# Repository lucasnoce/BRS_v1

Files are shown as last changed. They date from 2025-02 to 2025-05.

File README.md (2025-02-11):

# Basic Rocketry System

This repo will be used to develop a basic system for rocketry avionics. Development is still in initial phase, as described below, and will most definetly go under many changes and tweeks as the project evolves.

For updated project information, please refer to the [**General Requirements document**](Documentation/General_Requirements.pdf). The images and descriptions in this README may be out of date.

# Rocketry Overview
## My Background
I am a recently graduated Electronics Engineer and a space/rocketry enthusiast. For 3 years during graduation, I participated on a student rocketry team (at the time called Beyond Rocket Design, now Beyond Aerospace Department) where I helped to design and build model rockets for competitions like LASC, FBMF and so many others.

The problem is I knew nothing about rocketry back then (I still don't for the most part but hey, at least I have some xp now) and I was just starting to learn electronics, so although I knew how to code a little bit, I had never even heard of things like RTOS, threads, drivers and many many other things. Back then we used to program on Arduino IDE and created some really basic pcbs with ATmega328 and, later, ESP32 DevKit. Nothing wrong with that, we were able get somethings working, but of course my imagination never stops thinking about how much faster, reliable and efficient I could make those systems had I implemented them with some fancier techniques.

So, this is my main motivation for this project. I will be trying to implement an avionics system that does the basic but does it well. And obviously, if it works I will also try to convince the current team members to let me fly this thing on one of their rockets.

## Flight Behavior
Suborbital model rockets tend to (although, more often than desired, they don't) go through these 6 main stages during flight:
- Lift off
- Powered Ascent
- Coasting / Unpowered Ascent
- Parachute / Recovery system deployment
- Slow Descent
- Landing

<p align="center">
  <br>Flight Stages
  <br>Flight Stages (NASA)
  <br>Source: NASA's <a href="https://www1.grc.nasa.gov/beginners-guide-to-aeronautics/flight-of-a-model-rocket/" target="_blank">Beginners Guide to Aeronautics</a>
</p>
<!-- ![rktflight](https://github.com/user-attachments/assets/89e4ac4f-ced1-4a4b-8422-af78ff70ac67) -->

<p align="center">
  <br>Flight Stages: force analysis
  <br>Flight Stages Resultant Analysis
  <br>Source: Image created by the author
</p>
<!-- ![flight_stages](https://github.com/user-attachments/assets/95ef7178-a636-40cd-b9dc-83a80c350e83) -->

Notice that the most important events that happen during a flight - as far as software development goes - are the transitions between stages:
- Launch: transition from being still and moving, hopefully, upwards
- Main Engine Cut-Off (MECO): transition from Powered to Unpowered Ascent
- Apogee: transition from moving upwards to downwards
- Parachute: transition from descending almost on free fall to descending slowly
- Landing: transition from descending to - we expect - softly stopping on the ground

Consider that the avionics system will have some kind of IMU (Inertial Measurement Unit), which basically tells us the instantaneous acceleration along its 3 axes. It will also feature a barometric sensor to measure the air pressure during flight. Now, let's imagine a rocket flying without any rotation, so that the Z-axis is always pointing up (this will never actually happen, but it's good for demonstration purposes). We can plot a graph with the approximate resultant acceleration (in red) and the corresponding velocity (in green) during this flight.

<p align="center">
  <br>Flight Behavior: acceleration (red) and velocity (green)
  <br>Flight Behavior
  <br>Source: Image created by the author
</p>
<!-- ![desmos-graph](https://github.com/user-attachments/assets/daaf0ec1-653c-4937-aa67-dafecf62db17) -->

As we can see in this simplified example, the resultant acceleration starts at 0g (1g = 9.8 m/s^2). It rises up to about 5g and then falls back down to 0g. This period where the acceleration is positive corresponds to the powered ascent, as illustrated on the previous image. Note that the rocket hits its maximum velocity when the acceleration is 0 (of course, since a=dv/dt). Then, the vehicle experiences free fall for some time (a = -1g) until the parachutes are deployed, at around T+28 seconds. From this point, the rocket falls at a constant speed only to hit the ground at T+41 seconds.

Just to be very clear, this example is absolutely, completely inaccurate and overly simplified. In practice, the acceleration curve of the motor during powered ascent stage is much steeper and shorter and the free fall period should be significantly smaller. Also, this example ignores any kind of air resistance, which is definetely not a great idea when studying rockets. However, I hope the example helps us understand the overall behavior of a model rocket during flight.

# Project Requirements and definitions

For updated project information, please refer to the [**General Requirements document**](Documentation/General_Requirements.pdf). The images and descriptions in this README may be out of date.

## Hardware
The main objective with this project is to develop the device firmware, so hardware requirements are being defined based on components I have easy access to, mainly some off-the-shelf modules. If everything goes well after prototyping, I might review the project and design some proper hardware for it, but for now it is what it is.

## Firmware
First of all, I defined a [State Machine](Documentation/FW%20State%20Machine.png) to control the system behavior based on rockect flight phases. For this project, I considered that the parachute shall be deployed on apogee detection in order to simplify things a little. This machine will be managed by the Flight Control thread, shown in the [Architecture](Documentation/FW%20Architecture.png) structure below.

<p align="center">
  <br>FW State Machine
  <br>FW State Machine
  <br>Source: Image created by the author
</p>
<!-- ![FW State Machine](https://github.com/user-attachments/assets/7c7314bc-370f-4cdf-bbdf-a78096dcc1fc) -->

Basically, the system is initialized on the first state and, if everything is working properly, moves to S1 where the operation mode is selected based on a mechanical switch state. There are only 2 modes: UART mode is used to select secondary opModes (such as reading post-flight data and configuring the system) and Flight mode is where the magic happens.

A flight only starts after the Remove Before Flight tag is detected as removed. This has many reasons, in this case the most important being reliability, since this helps prevent a false flight start, as well as saving battery power. After that, the system has 4 detection states, one for each flight stage transition. For example, S3 keeps trying to detect lift off stage by analyzing IMU and barometric sensor data. Another example is S4, which tries to detect MECO by also analysing data from IMU and barometric sensor, or (for redundancy) can move forward after a certain timeout.

After landing has been detected (and if the rocket is still a rocket) the system tries to backup the data from internal flash to a secondary storage unit, which may be a microSD card or another flash chip (still to be defined). Finally, the system goes to S8, a state designed to facilitate rocket recovery (sometimes, they really like hiding underground) while also saving battery power. In this state, the system stays on a cycle of sleeping and waking up to beep/blink the buzzer/LEDs until the battery is critically low.

All of this is operation is illustrated in the following [Flowchart](Documentation/FW%20Flowchart.png) (also under development).

<p align="center">
  <br>FW Flowchart
  <br>FW Flowchart
  <br>Source: Image created by the author
</p>
<!-- ![FW Flowchart](https://github.com/user-attachments/assets/43fa580d-00c4-4f8f-b531-e44d9dea57e4) -->

Lastly, the system will be organized according to the following [Architecture](Documentation/FW%20Architecture.png) (yes, you guessed it, this is also not the final version).

<p align="center">
  <br>FW Architecture
  <br>FW Architecture
  <br>Source: Image created by the author
</p>
<!-- ![FW Architecture](https://github.com/user-attachments/assets/24211131-3822-4550-bf50-66789afae103) -->

## Tests and Validation
Untested rocket code is bad rocket code. So, I need a good way of testing this firmware to validate individual blocks and also the complete system working together. Of course, the biggest issue here is that I don't have multiple rockets to fire up and watch what happens. I am still not sure how to do this (if you have any ideas or advices, please tell me), but I fell like what I need is a combination of these 2 things:
1. Simulated flight data: a piece of code that simulates a flight by generating coherent sensor data and feeds it into the system firmware as inputs.
2. Small scale test flight: some sort of physical structure tied to my device/pdb that allows me to through it up the air and control the descent phase so that it doesn't crash onto the ground.

First method is clearly safer, but doesn't provide a "real world" condition. Second method allows me to test things in conditions closer to a real flight, but may lead to a lot of frustration, electronic waste and emptiness in my wallet. For now though, I will focus on developing the main firmware and some sort of flight simulation function.

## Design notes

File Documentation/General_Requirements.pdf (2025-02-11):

# Basic Rocket System v1.0

## General Requirements and Specification

Rev 01
2025

Lucas Arturo Noce
lucasnoce0@gmail.com
https://github.com/lucasnoce/BRS_v1

Table of Contents

List of Figures

List of Tables

### 1. Document overview

1.1. Introduction

The Basic Rocket System (BRS) is an open source device designed - as a side personal project - to implement all the most basic functionalities expected from a model rocket avionics computer.
The focus of the project is on firmware development, as hardware is heavily dependent on the rocket structure and design. However, firmware does not exist without hardware, so a block diagram and electrical schematic will be sketched. The system will be designed to feature some basic functionalities and also to be compatible with future software and, especially, hardware upgrades that can provide further utilities for the system.
1.2. Scope

This document aims to clearly define all the BRS requirements, such as hardware and firmware structure, and also describe guidelines of how the system should perform and be built.
In this document, some main hardware components will also be specified to allow firmware development to be started. The complete electrical schematic and PCB layout are topics for another document.
1.3. Disclaimer

This project is designed by me, Lucas, as a personal project. It is not intended for commercial purposes nor any other use rather than model rocketry hobby activities.
This project is open-source under the MIT license, allowing the community to explore and contribute. However, I disclaim any responsibility for any misuse, damage, or consequences resulting from the use of this project. Do it at your own risk.
Rockets can be seriously dangerous - and potentially deadly - for the ones involved, for others and nearby strangers, so be very cautious, conservative and safe when exploring the rocketry world.

### 2. Hardware Requirements

2.1. MoSCoW Analysis

The definition of HW specification started by listing all the components related to a standard avionics system. Then, the MoSCoW prioritisation method was implemented in order to enumerate the necessary and desired components. The criteria used to categorize each component was completely arbitrary, but focused on maintaining the lowest possible cost while also allowing the device to have all the key features needed for a basic avionics system.

Table 1 - Hardware Components MoSCoW Analysis

Hardware Component | MoSCoW | Comments
MCU | Must Have | Focus on low power and/or low cost
IMU | Must Have | Periodically sample acceleration and gyro
Barometer | Must Have | Apogee detection
Power Tree | Must Have | Includes power source, probably LiPo batteries
Recovery System | Must Have | For triggering parachute deployment
Data logging | Must Have | Primarily flash chip, maybe microSD card for cost reduction
Remove Before Flight | Must Have | Must be removed with the rocket fully assembled
LEDs | Must Have | Indicate system state
Backup System | Should Have | May not be designed for cost reduction
Buzzer | Should Have | Indicate system state
GPS | Should Have | May not be used for cost reduction
Wireless Communication | Should Have | Will likely be added later, probably LoRa P2P
Camera | Could Have | Really increases system complexity and storage demand, may be added later as a separate system
Self Ignition System | Could Have | Depends on rocket motor design

Because of the mentioned criteria, some important components were categorized as “Should Have” or even “Could Have” to reduce costs. But, as the project evolves, some of them may be added on later versions of the system.
After the MoSCoW analysis, the components chosen to integrate the project are the following:
- MCU
- IMU

- Barometer
- Power Tree
- Recovery System
- Data logging
- Remove Before Flight
- LEDs
- Buzzer
2.2. Components Specification

Considering that the device will not be mass produced, many components were chosen based on availability, meaning that the focus on low power and/or low cost are often more dependent on retailers stock than on datasheet information.

### 2.2.1. MCU

For the MCU, the following options were considered. Component information was sourced from the corresponding datasheet. Average price is an approximate value taken from local stores.

Table 2 - MCU Options

Manufacturer | Part # | Flash / RAM (bytes) | Max Clock (MHz) | Consumption (mA@freqmax) | Average Price
STMicroelectronics | STM32F103C8 | 64k / 20k | 72 | 50 | R$ 30,00
STMicroelectronics | STM32F103RB | 128k / 20k | 72 | 50 | R$ 100,00
STMicroelectronics | STM32F401CC | 256k / 64k | 84 | 22 | R$ 45,00
STMicroelectronics | STM32F411CE | 512k / 128k | 100 | 23.6 | R$ 55,00
Espressif | ESP32-WROOM-32 | 4M / 520k | 240 | 80 | R$ 40,00

Data driven analysis indicates that the best option (low cost, high density) would be the ESP32. However, previous experiences were also considered and I happen to not be a huge fan of the Espressif platform. Besides, the datasheet shows an average current consumption of 80 mA, which is the highest value amongst the options.
The second best component seems to be the STM32F411CE, which has enough flash memory to store data from one entire flight and the largest RAM compared to the remaining options. That, alongside presenting almost a quarter of the current consumption than the ESP32, has made this the selected MCU.

### 2.2.2. IMU

For the IMU, the following options were considered. Component information was sourced from the corresponding datasheet. Average price is an approximate value taken from local stores.

Table 3 - IMU Options

Manufacturer | Part # | DOF | Max Acc ODR (Hz) | Max Acc Range | Supply Voltage | Consumption | Bus | Average Price
NXP | MMA8452 | 3 | 800 | ±8g | 2.0~3.6V | <165 μA | I2C | R$ 20,00
InvenSense | MPU6050 | 6 | 1k | ±16g | 2.4~3.4V | <3.9 mA | SPI / I2C | R$ 30,00
STM | LSM6DS3 | 6 | 1.6k | ±16g | 1.7~3.6V | <900 μA | SPI / I2C | R$ 20,00
Bosch | BNO055 | 9 | 100 | ±16g | 2.4~3.6V | <12.3mA | I2C / UART | R$ 300,00

The first version will use an MPU6050 for its good overall balance of features and cost, as well as being a fairly common and off the shelf option. That said, later versions may switch to the LSM6DS3, as it seems to be a little more adequate for the task based on having a greater ODR and lower current consumption, while maintaining a similar price.

### 2.2.3. Barometer

Table 4 - BAR Options

Manufacturer | Part # | Pressure Resolution | Pressure Range (hPa) | ODR (Hz) | Consumption | Bus | Average Price
Bosch | BMP180 | 1 Pa | 300~1100 | 120 | <12 μA | SPI / I2C | R$ 10,00
Bosch | BMP280 | 0.16 Pa | 300~1100 | 157 | <2.8 μA | SPI / I2C | R$ 20,00
Bosch | BME280 | 0.18 Pa | 300~1100 | 182 | <2.8 μA | SPI / I2C | R$ 20,00
STM | LPS22HH | 0.02 Pa | 260~1260 | 200 | <4 μA | SPI / I2C | R$ 6,00

The first version will use a BMP280 for its good overall balance of features and cost, as well as being a fairly common and off the shelf option. That said, later versions may switch to the LPS22HH, as it seems to be a little more adequate for the task based on having a greater ODR and similar current consumption and price.

### 2.2.4. Power Tree

The Power Tree (PWT) is actually a subcircuit that contains all power supply components, as well as the control signals and other power related items. As of the first version of this system, the PWT block diagram is as follows. The red arrows indicate power delivery traces and the grey ones indicate signal traces.

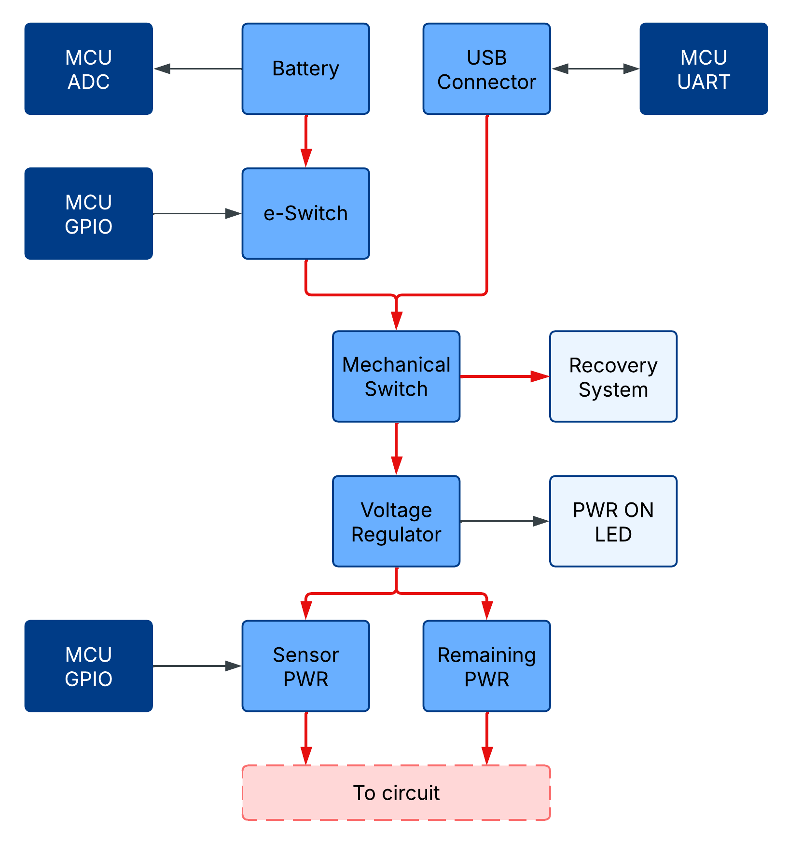
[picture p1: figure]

Figure 1 - Power Tree block Diagram

The subcircuit provides two ways of powering the device: internal battery and USB connector. To prevent issues with both power sources connected at the same time, protective diodes must be added accordingly and an SMD solder jumper should be added to allow physical disconnection of the USB power line to the system, still granting serial communication through GND and UART traces.
The internal battery must be able to provide the voltage and current necessary to the system through the whole flight process, including the periods between system power up and the actual vehicle launch and between landing and physical recovery of the rocket. Both of these periods are unknown beforehand and prone to several minutes or hours of delay, depending on a variety of factors such as weather conditions, unexpected on-site issues, etc.
With that in mind, it is important to calculate, simulate and test a large number of scenarios in order to correctly specify the minimum battery capacity needed, which will only be possible to do reliably after the whole system is working properly. Thus, the current capacity of the internal battery will be defined later on. The voltage however, depends on two main factors: the voltage regulator constraints and the recovery system design. The first factor will probably not be an issue, as the voltage regulator selected will most certainly be a switching regulator, which typically accepts a wide range of input voltage.
The recovery system design can vary a lot. In my previous experience, this system was quite unusual and deployed the parachutes from a side door on the body of the rocket without the use of any explosive. Instead, it used some electromagnets to hold a metal piece fixated on the side door. This design is interesting for not using explosives, but continuously drains current from the power supply to keep the doors closed and also requires higher voltages to properly activate the electromagnets.
A more common approach is to divide the rocket into two (or more) parts and position the parachutes on the nose cone. Some sort of explosive is then used to separate these parts and deploy the recovery system. In this method, despite having some associated risk related to the explosive, the power demand is significantly smaller, since the system only uses power momentarily to ignite the explosive.
There are plenty of other designs and philosophies regarding recovery systems. To simplify things a little, this project will use a 12V battery source, which is a fairly common value and may be compatible with most recovery system designs.
Back to the PWT subcircuit, some details are important to guarantee a successful flight and to improve avionics system handling on a fully assembled rocket. For that, the PWT design shall follow the guidelines:
- ON/OFF mechanical switch must be accessible from outside with the rocket fully assembled;
- PWT subcircuit shall not feature battery charging for the sake of simplicity;
- USB connector shall be either type C (preferably) or microB;
- A solder jumper must be added to select between power sources, i.e. a jumper footprint on the USB power line right before the Mechanical Switch, effectively allowing the disconnection of the USB power supply;
- The system must implement a self-shutdown feature controlled by MCU, through the e-Switch;
- The voltage regulator must be able to provide enough power for all transient events that are known;
- It is advisable that the implemented regulator follows a switching topology for better overall performance;
- The MCU must be able to control the power delivery (ON/OFF) to the “sensors” (IMU, BAR and backup flash);

### 2.2.5. Recovery System

// TODO

### 2.2.6. Storage

The first analysis that needs to be done regarding a storage solution is to estimate how much data a typical flight will generate. To do that, the following data structure is considered, taking into consideration the selected sensors characteristics.

Table x - Components Summary

Component | Data | Type | Unit | Estimate Size (bytes)
MCU | Timestamp | uint32_t | ms | 4
MCU | Flight State | uint8_t | - | 1
MCU | Device Status | uint8_t | - | 1
MCU | Battery Voltage | uint16_t | mV | 2
IMU | Accelerometer | uint16_t [3] | raw | 6
IMU | Gyroscope | uint16_t [3] | raw | 6
BAR | Pressure | uint8_t [3] | raw | 3
BAR | Temperature | uint8_t [3] | raw | 3
Total | | | | 26

// TODO

### 2.2.7. Remove Before Flight

// TODO
- Must be accessible from outside, i.e. with the rocket fully assembled
- Must be possible to reinsert the tag with the rocket fully assembled

### 2.2.8. LEDs and Buzzers

To define the number of LEDs necessary to the system, the following reasoning was presented:
- FW predicts a total of 11 states on State Machine, so a 4 LEDs can display the current state (for debugging only, they may be removed for flight)
- 1 LED for power input indication (purely HW, may be removed for flight)
- 1 LED for low battery indication
- At least 2 more LEDs for other indications and debugging

With this in mind, a total of 8 LEDs can comfortably handle all the needs of the system. Since one of them is not controlled by the MCU, there are 7 LEDs left to be controlled. Using one dedicated GPIO for each LED is poor use of resources and can lead to unnecessary future constraints on the hardware side, so a better option is to control the LEDs through an I2C IO Expander. And because these ICs typically provide a power-of-two number of IOs, one more LED will be added to complete 8 controlled LEDs and 1 uncontrolled LED.
For the expander, some options were considered and the selected IC was the TCA9534A by Texas Instruments, since it provides all the needs for this task as well as being the cheapest option.
The buzzer, on the other hand, can’t be efficiently used through an IO Expander, since it requires PWM output for better control. Hence, it will be connected to a dedicated PWM-capable GPIO. Also, only one buzzer will be used, since there are only 3 use cases predicted, which don’t interfere with each other:
- Signaling RBF
- Facilitate recovery process (keeps beeping after landing)
- Low battery indication

Finally, it is worth noting the suggestion to add a low pass filter between the PWM GPIO and the buzzer input to increase sound quality.

### 2.2.9. Components Summary

Finally, a summary of all selected components and corresponding specification is presented below. This list is still not a Bill Of Materials, so only the most important components are shown.

Table x - Components Summary

Component | Specification
MCU | STM32F411CE
IMU | MPU6050
BAR | BMP280
Power Tree | 12V battery, USB, ON/OFF switches
Recovery | // TODO
Backup Flash | // TODO
RBF | // TODO
LEDs | 8 LEDs through TCA9534A IO expander
Buzzer | 1 buzzer
2.3. Block Diagram

Based on the selected components, a high abstraction block diagram was designed to help visualize the circuits. Grey arrows indicate signal traces, while the green ones indicate high voltage and red ones low voltage power delivery traces.

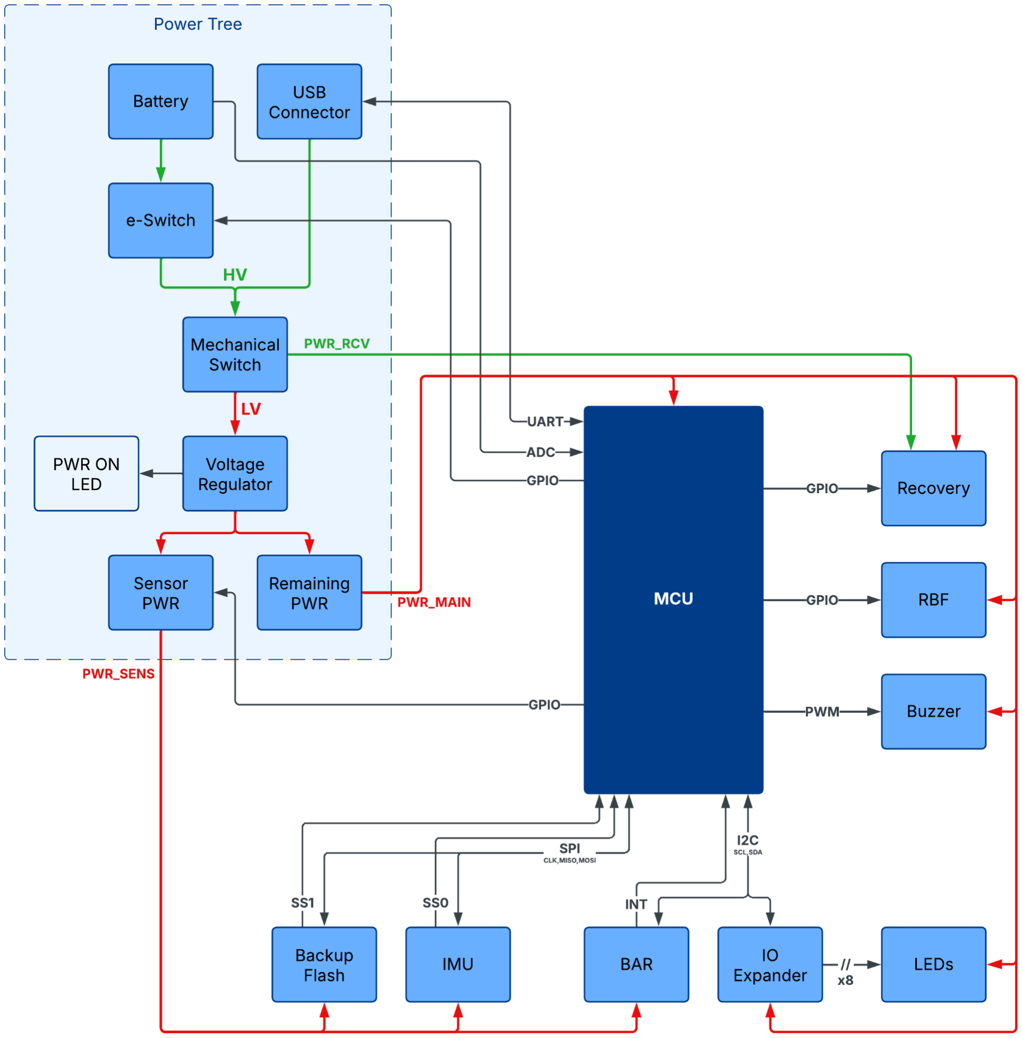
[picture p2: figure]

Figure 2 - Circuit Block Diagram

### 3. Software Requirements

3.1. State Machine

A state machine was created to better organize and control the device under all the possible flight stages and implement other functionalities.

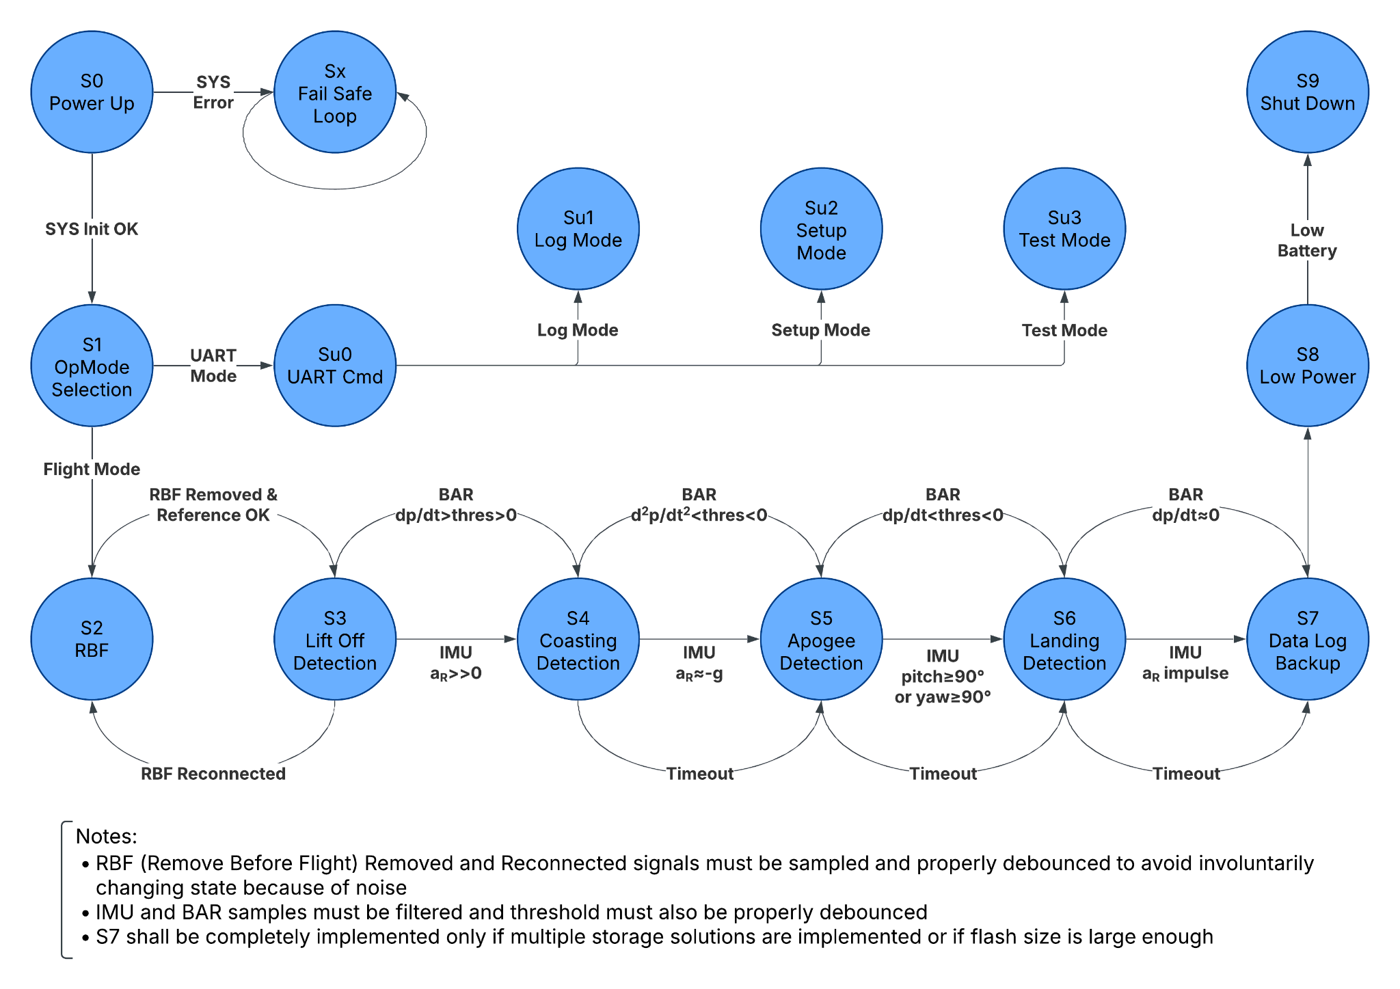
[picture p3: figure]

Figure 3 - System State Machine

### 3.1.1. S0 - Power Up

This is the first state of the system after being powered up. It carries the responsibility of initializing all the drivers and services necessary for device operation.
Since the system can wake up after a variety of events - and, therefore, have valuable data stored in flash memory - the S0 state is also responsible for reading some system status information from flash and deciding how to move forward with the operation from a safety perspective. It should be able to detect, for example, if the system is booting up mid flight after some unexpected shutdown has happened and after that, try to resume operation from the previously known state.

### 3.1.2. S1 - OpMode Selection

This state is responsible for determining the selected operation mode based on a physical switch/jumper. There are 2 operation modes:
- Flight mode corresponds to a secondary state machine which tracks the flight stages based on sensor readings. It consists of states S2 through S7.
- UART mode is meant to select between the secondary operation modes through custom AT commands.

The operation mode selection is designed this way (mixing hardware and software selections) to minimize the chance of an undesired operation mode swap during flight caused by vibration. This design only allows the selection of a secondary mode (Sun

) when the hardware selection jumper is wired correctly.

### 3.1.3. S2 - Remove Before Flight

This state is the first step of the flight mode. It continuously tries to identify if the Remove Before Flight (RBF) tag has been removed, indicating that the vehicle is completely assembled and ready to launch. This is done by polling the corresponding RBF GPIO input value and getting the RBF removed value for many times in a row.
Also in this state, right after the RBF removal is detected, some reference measures are taken and used as a starting point for the flight, such as vehicle attitude (inclination of the rocket), vehicle orientation (the axes with the largest acceleration magnitude), ground level pressure, etc. These measures must be successfully completed in order for the machine to advance to the next state, otherwise it must indicate this error and stop the launch procedure for vehicle inspection and system reboot.

### 3.1.4. S3 - Lift Off Detection

After S2 is completed, the machine enters a lift off detection state. In this state, the system effectively starts to read, interpret and store data from the sensors continuously with the objective of detecting the motor ignition. These are the possible signals that can trigger a state change (in order of priority):
- RBF reconnected: if the RBF is reconnected, the system will understand it as a launch hold and return to the previous state (S2).
- IMU resulting acceleration values show a sudden and intense increase in magnitude while also inverting the signal value of the vertical orientation axes (previously determined).
- BAR readings show a sudden, intense and consistent decrease in magnitude, indicating a sequential drop in pressure, thus a rise in altitude.

### 3.1.5. S4 - Coasting Detection

After successfully detecting lift off, the system moves to S4 which aims to detect the ending of powered ascent and beginning of coasting phase. For this to happen, these triggers are considered (in order of priority):
- IMU resulting acceleration values show a consistent decrease in magnitude (tending to the previously determined baseline value of approximately -1g) while also inverting the signal value of the vertical orientation axes again.
- BAR readings show a growing decrease in magnitude (approximately constant decrease of second derivative), indicating a sequential drop in pressure, thus a rise in altitude
- A coasting detection timeout occurs (empirically determined and implemented in pre-compile time).

### 3.1.6. S5 - Apogee Detection

After successfully detecting coasting, the system moves to S5 which aims to detect apogee, i.e. the ending of ascent and beginning of descent phase. For this to happen, these triggers are considered (in order of priority):
- BAR readings show a consistent increase in magnitude, indicating a sequential rise in pressure, thus a drop in altitude. Can also be understood as a change in slope signal of the pressure variation.
- IMU gyroscope values show an absolute rotation above 90° in pitch (θ) or yaw (φ), not considering rotation around the previously determined vertical orientation axes, roll (ζ).
- An apogee detection timeout occurs (empirically determined and implemented in pre-compile time).

### 3.1.7. S6 - Landing Detection

After successfully detecting apogee, the system moves to S6 which aims to detect landing. For this to happen, these triggers are considered (in order of priority):

- BAR readings show consistently similar magnitude values, indicating steady pressure levels, thus a stable and constant altitude.
- IMU resulting acceleration values show a short impulse magnitude (full scale) followed by constant values of around 1g.
- A landing detection timeout occurs (empirically determined and implemented in pre-compile time).

### 3.1.8. S7 - Data Log Backup

After landing detection, the system enters Data Log Backup state, which can be skipped if there are no backup storage devices detected. This state copies the contents of the internal storage into the backup storage for redundancy and ease of access, especially if the backup device is an SD card.

### 3.1.9. S8 - Low Power

After backing up the stored flight data, the system goes to Low Power state, where it deinitializes all the unnecessary drivers and services and enters a light sleep loop. In this loop, the device keeps blinking an indication LED and beeping the buzzer for some period to help find the vehicle on the recovery mission.
This loop continues until a low voltage threshold is reached on the ADC readings of the internal battery. After that, the machine moves to the S10 state.

### 3.1.10. S9 - Shut Down

In this state, the system executes a self-shutdown procedure. This procedure triggers a MOSFET to essentially disconnect the internal battery (main power source during flight) from the power supply line, which turns the device completely off.

### 3.1.11. Sx - Fail Safe

This is a fail safe state, designed to safely and reliably manage system initialization errors, allowing unexpected behavior to be handled in a controlled and harmless way.

### 3.1.12. Su0 - UART Command

This state corresponds to UART Command, which allows the user to select between the secondary operation modes through custom serial port AT commands.

### 3.1.13. Su1 - Log Mode

This state corresponds to a read-only state where stored flight data can be safely accessed and retrieved from internal and/or backup storage.

### 3.1.14. Su2 - Setup Mode

This state allows the user to set up the device configuration.

### 3.1.15. Su3 - Test Mode

This state is meant to be used as a Test mode for the device, yet to be completely defined.

3.2. Flowchart

Based on the state machine, the following firmware flowchart was designed.

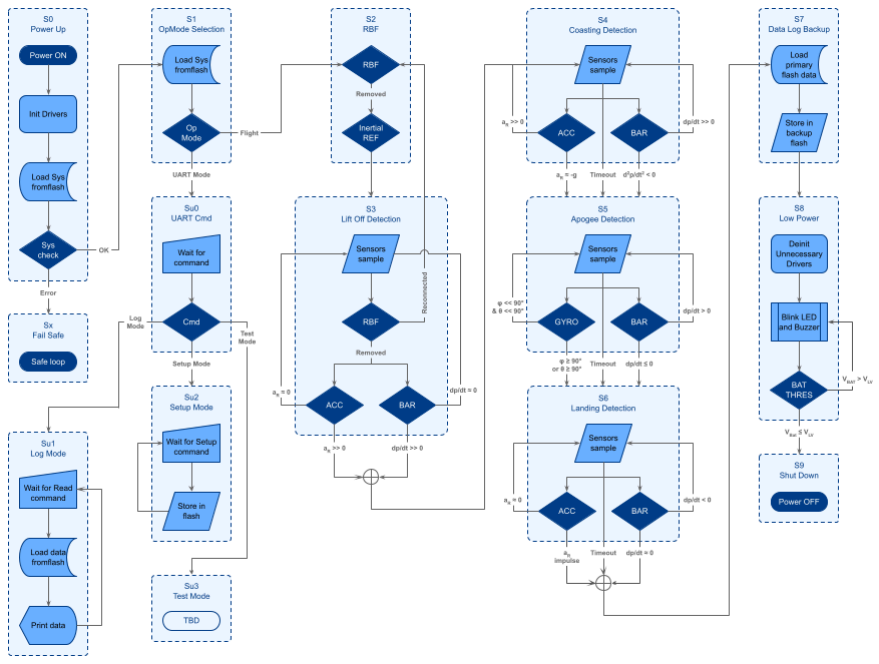
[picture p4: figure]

Figure 4 - Firmware Flowchart

3.3. Firmware Architecture

The firmware abstraction layers are organized as illustrated below. The MCU HAL layer is provided by STM32CubeMX and allows the use of MCU hardware. Above the MCU HAL, a Board Support Package provides an isolation layer between the BRS and hardware specific functions, essentially granting a high level of compatibility between the whole software above and almost any other MCU with minimal driver refactoring.
The Drivers layer implements all the necessary drivers for the suggested hardware approach mentioned in the previous section. This layer is then consumed by the Services layer, which manages all the necessary activities needed. Finally, a high level Application layer implements the designed state machine. Between the Services and Application layers is the Inter Process Communication service which provides a messaging system for threads of both layers to communicate through. The RTOS used will be FreeRTOS.

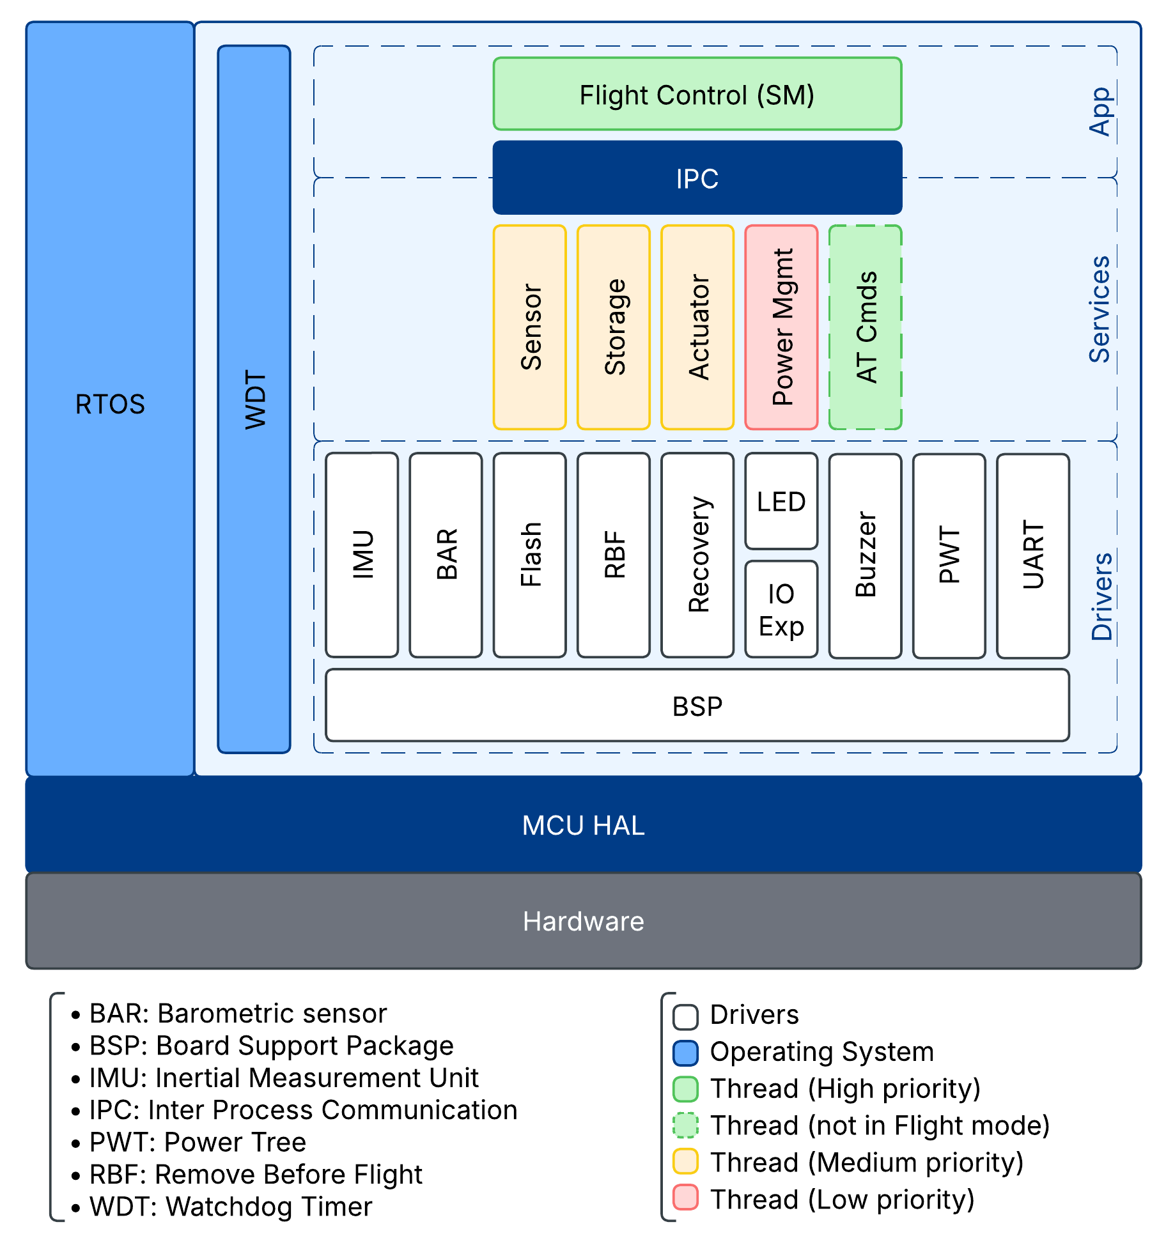
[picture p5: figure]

Figure 5 - Firmware Layer Architecture

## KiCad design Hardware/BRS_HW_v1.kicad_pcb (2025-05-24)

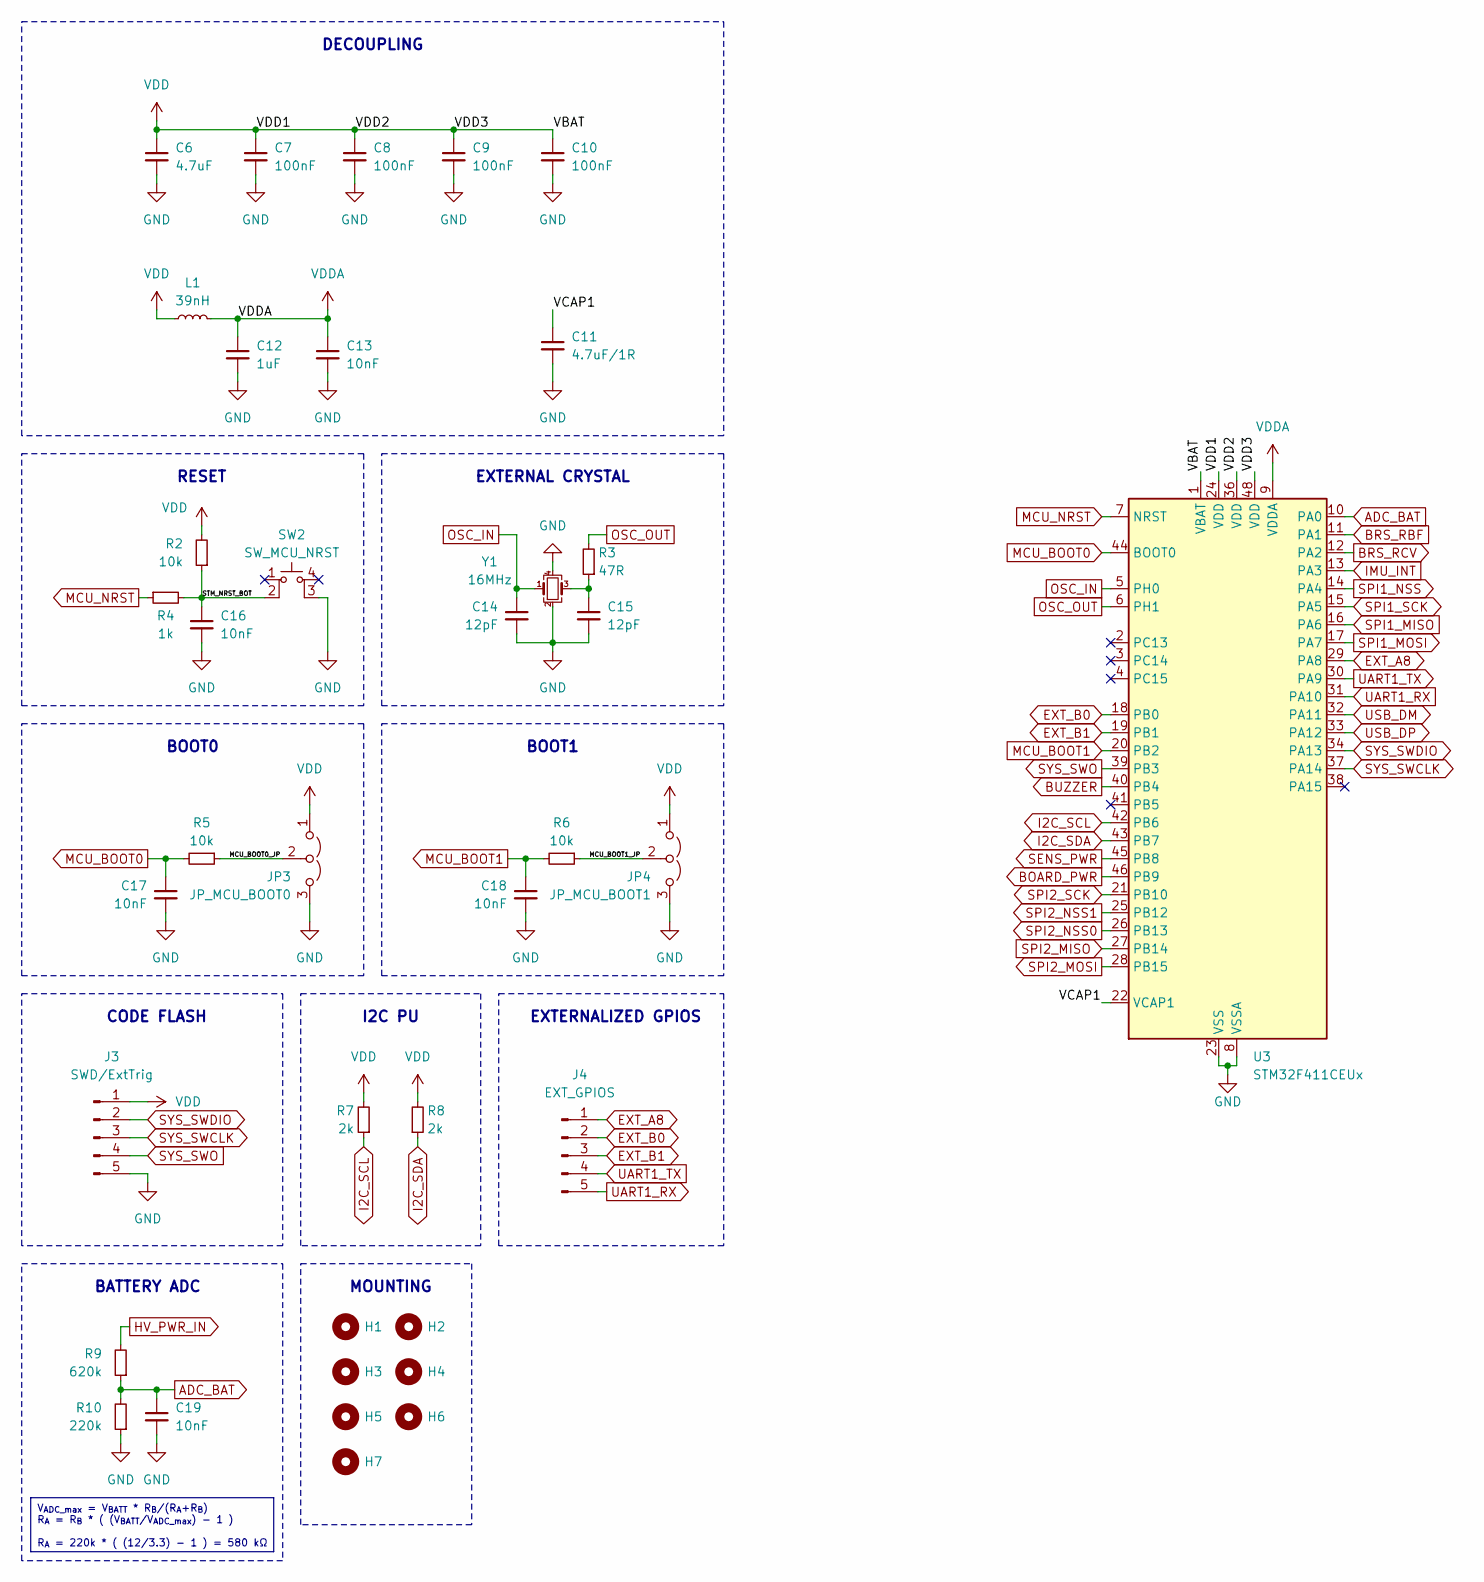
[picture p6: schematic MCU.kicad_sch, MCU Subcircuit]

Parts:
C6: 4.7uF; C_0603_1608Metric; LCSC Part Number C19666
C7, C8, C9, C10: 100nF; C_0402_1005Metric; LCSC Part Number C1525
C11: 4.7uF/1R; C_0603_1608Metric; LCSC Part Number C57112
C12: 1uF; C_0402_1005Metric; LCSC Part Number C52923
C13: 10nF; C_0402_1005Metric; LCSC Part Number C15195
C14, C15: 12pF; C_0402_1005Metric; LCSC Part Number C1547
C16, C17, C18, C19: 10nF; C_0603_1608Metric; LCSC Part Number C57112
H1, H3, H5, H7: SupPCB; MountingHole_2.2mm_M2_DIN965
H2, H4, H6: ToolingHole; JLCPCB_Tooling_Hole
J3: SWD/ExtTrig; PinHeader_1x05_P2.54mm_Vertical
J4: EXT_GPIOS; PinHeader_1x05_P2.54mm_Vertical
JP3: JP_MCU_BOOT0; SMD_SolderJumper_Triple_Small
JP4: JP_MCU_BOOT1; SMD_SolderJumper_Triple_Small
L1: 39nH; L_0603_1608Metric
R2, R5, R6: 10k; R_0603_1608Metric; LCSC Part Number C25804
R3: 47R; R_0402_1005Metric; LCSC Part Number C25120
R4: 1k; R_0603_1608Metric; LCSC Part Number C21190
R7, R8: 2k; R_0402_1005Metric; LCSC Part Number C22975
R9: 620k; R_0603_1608Metric; LCSC Part Number C22975
R10: 220k; R_0603_1608Metric; LCSC Part Number C22975
SW2: SW_MCU_NRST; SW_TS-1187A-B-A-B; LCSC C318884
U3: STM32F411CEUx; QFN-48-1EP_7x7mm_P0.5mm_EP5.6x5.6mm
Y1: 16MHz; Crystal_SMD_Abracon_ABM8G-4Pin_3.2x2.5mm; LCSC Part Number C13738

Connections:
/MCU/MCU_BOOT0_JP: JP3.2 (C), R5.1
/MCU/MCU_BOOT1_JP: JP4.2 (C), R6.1
/MCU/STM_NRST_BOT: C16.1, R2.1, R4.2, SW2.2
/MCU/VCAP1: C11.1, U3.22 (VCAP1)
ADC_BAT: C19.1, R9.1, R10.2, U3.10 (PA0)
BOARD_PWR: U3.46 (PB9); also elsewhere on the board
BRS_RBF: U3.11 (PA1); also elsewhere on the board
BRS_RCV: U3.12 (PA2); also elsewhere on the board
BUZZER: U3.40 (PB4); also elsewhere on the board
EXT_A8: J4.1, U3.29 (PA8)
EXT_B0: J4.2, U3.18 (PB0)
EXT_B1: J4.3, U3.19 (PB1)
GND: C6.2, C7.2, C8.2, C9.2, C10.2, C11.2, C12.2, C13.2, C14.2, C15.2, C16.2, C17.2, C18.2, C19.2, J3.5, JP3.3 (B), JP4.3 (B), R10.1, SW2.3 (K), U3.8 (VSSA), U3.23 (VSS), U3.35 (VSS), U3.47 (VSS), U3.49 (VSS), Y1.2, Y1.4; also elsewhere on the board
HV_PWR_IN: R9.2; also elsewhere on the board
I2C_SCL: R7.1, U3.42 (PB6); also elsewhere on the board
I2C_SDA: R8.1, U3.43 (PB7); also elsewhere on the board
IMU_INT: U3.13 (PA3); also elsewhere on the board
MCU_BOOT0: C17.1, R5.2, U3.44 (BOOT0)
MCU_BOOT1: C18.1, R6.2, U3.20 (PB2)
MCU_NRST: R4.1, U3.7 (NRST)
unnamed: C15.1, R3.1, Y1.3
OSC_IN: C14.1, U3.5 (PH0), Y1.1
OSC_OUT: R3.2, U3.6 (PH1)
SENS_PWR: U3.45 (PB8); also elsewhere on the board
SPI1_MISO: U3.16 (PA6); also elsewhere on the board
SPI1_MOSI: U3.17 (PA7); also elsewhere on the board
SPI1_NSS: U3.14 (PA4); also elsewhere on the board
SPI1_SCK: U3.15 (PA5); also elsewhere on the board
SPI2_MISO: U3.27 (PB14); also elsewhere on the board
SPI2_MOSI: U3.28 (PB15); also elsewhere on the board
SPI2_NSS0: U3.26 (PB13); also elsewhere on the board
SPI2_NSS1: U3.25 (PB12); also elsewhere on the board
SPI2_SCK: U3.21 (PB10); also elsewhere on the board
SYS_SWCLK: J3.3, U3.37 (PA14)
SYS_SWDIO: J3.2, U3.34 (PA13)
SYS_SWO: J3.4, U3.39 (PB3)
UART1_RX: J4.5, U3.31 (PA10)
UART1_TX: J4.4, U3.30 (PA9)
USB_DM: U3.32 (PA11); also elsewhere on the board
USB_DP: U3.33 (PA12); also elsewhere on the board
VDD: C6.1, C7.1, C8.1, C9.1, C10.1, J3.1, JP3.1 (A), JP4.1 (A), L1.1, R2.2, R7.2, R8.2, U3.1 (VBAT), U3.24 (VDD), U3.36 (VDD), U3.48 (VDD); also elsewhere on the board
VDDA: C12.1, C13.1, L1.2, U3.9 (VDDA)

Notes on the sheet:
V_{ADC_max} = V_{BATT} * R_{B}/(R_{A}+R_{B}) R_{A} = R_{B} * ( (V_{BATT}/V_{ADC_max}) - 1 ) R_{A} = 220k * ( (12/3.3) - 1 ) = 580 kΩ
BOOT1
MOUNTING
CODE FLASH
EXTERNAL CRYSTAL
I2C PU
DECOUPLING
BOOT0
EXTERNALIZED GPIOS
BATTERY ADC
RESET

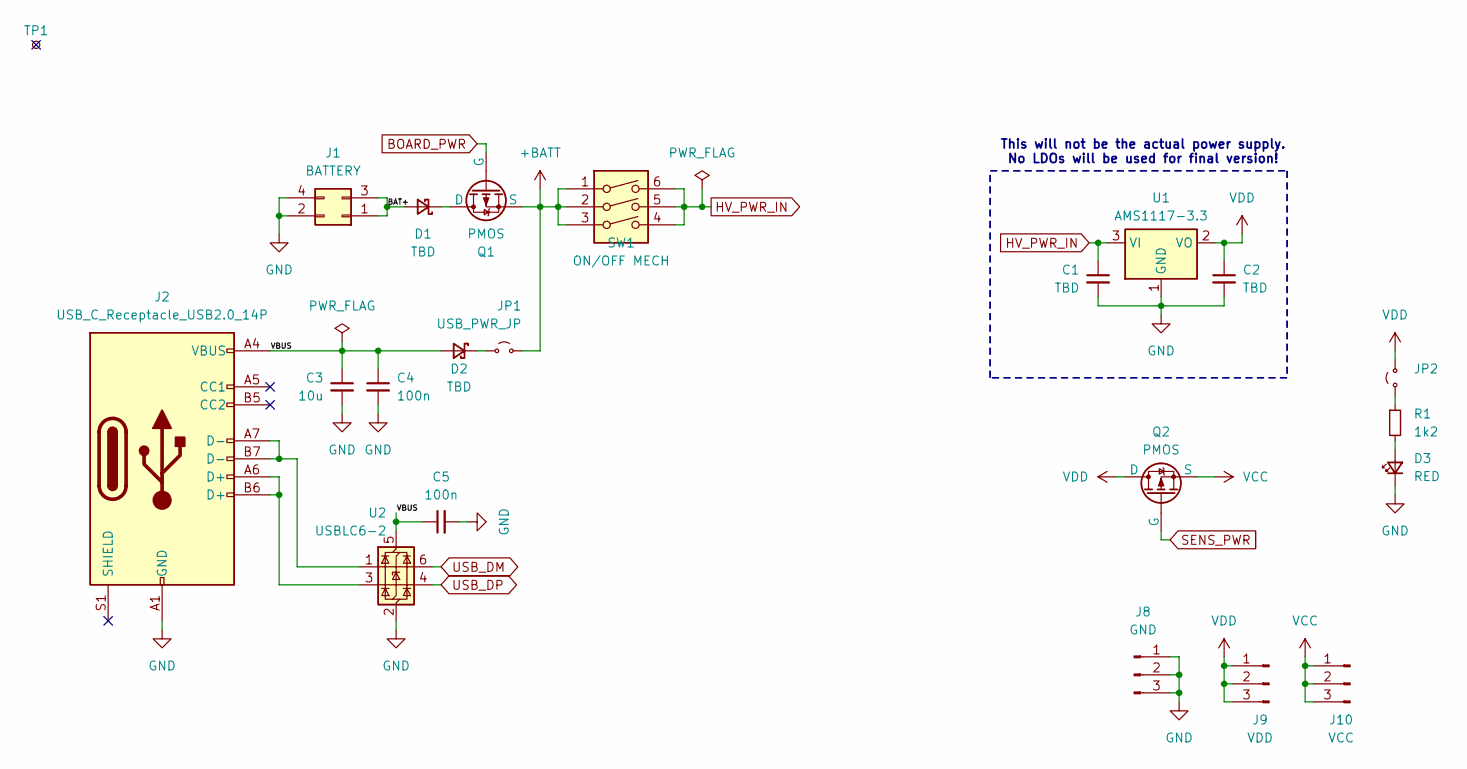
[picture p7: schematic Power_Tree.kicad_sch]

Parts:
C1, C2: TBD; C_0603_1608Metric
C3: 10u; C_0603_1608Metric
C4, C5: 100n; C_0603_1608Metric
D1, D2: TBD; D_SOD-123
D3: RED; LED_0603_1608Metric
J1: BATTERY; Molex_Micro-Fit_3.0_43045-0412_2x02_P3.00mm_Vertical
J2: USB_C_Receptacle_USB2.0_14P; USB_C_Receptacle_GCT_USB4105-xx-A_16P_TopMnt_Horizontal
J8: GND; PinHeader_1x03_P2.54mm_Vertical
J9: VDD; PinHeader_1x03_P2.54mm_Vertical
J10: VCC; PinHeader_1x03_P2.54mm_Vertical
JP1: USB_PWR_JP; SolderJumper-2_P1.3mm_Open_RoundedPad1.0x1.5mm
JP2: Jumper_2_Small_Open; SMD_SolderJumper_Small
Q1, Q2: PMOS; SOT-23
R1: 1k2; R_0603_1608Metric
SW1: ON/OFF MECH; SW_DIP_SPSTx03_Slide_6.7x9.18mm_W7.62mm_P2.54mm_LowProfile
TP1: TestPoint_Small; TestPoint_Pad_D1.5mm
U1: AMS1117-3.3; SOT-223-3_TabPin2
U2: USBLC6-2; SOT-23-6

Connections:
+BATT: JP1.2 (B), Q1.3 (S), SW1.1, SW1.2, SW1.3
/Power_Tree/BAT+: D1.2 (A), J1.1, J1.3
/Power_Tree/VBUS: C3.1, C4.1, C5.1, D2.2 (A), J2.A4 (VBUS), J2.A9 (VBUS), J2.B4 (VBUS), J2.B9 (VBUS), U2.5 (VBUS)
BOARD_PWR: Q1.2 (G); also elsewhere on the board
GND: C1.2, C2.2, C3.2, C4.2, C5.2, D3.1 (K), J1.2, J1.4, J2.A1 (GND), J2.A12 (GND), J2.B1 (GND), J2.B12 (GND), J8.1, J8.2, J8.3, U1.1 (GND), U2.2 (GND); also elsewhere on the board
HV_PWR_IN: C1.1, SW1.4, SW1.5, SW1.6, U1.3 (VI); also elsewhere on the board
unnamed: D1.1 (K), Q1.1 (D)
unnamed: D2.1 (K), JP1.1 (A)
unnamed: D3.2 (A), R1.2
unnamed: J2.A6 (D+), J2.B6 (D+), U2.3 (I/O2)
unnamed: J2.A7 (D-), J2.B7 (D-), U2.1 (I/O1)
unnamed: JP2.1 (A), R1.1
SENS_PWR: Q2.2 (G); also elsewhere on the board
USB_DM: U2.6 (I/O1); also elsewhere on the board
USB_DP: U2.4 (I/O2); also elsewhere on the board
VCC: J10.1, J10.2, J10.3, Q2.3 (S); also elsewhere on the board
VDD: C2.1, J9.1, J9.2, J9.3, JP2.2 (B), Q2.1 (D), U1.2 (VO); also elsewhere on the board

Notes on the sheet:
This will not be the actual power supply. No LDOs will be used for final version!

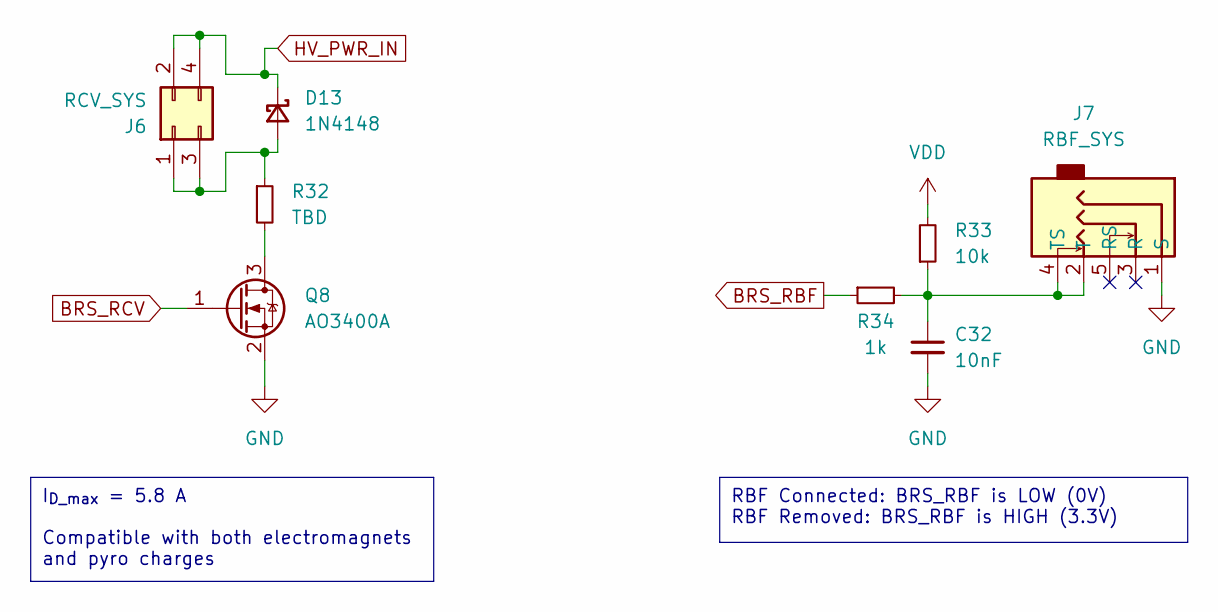
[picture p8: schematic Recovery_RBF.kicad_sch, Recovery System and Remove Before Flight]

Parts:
C32: 10nF; C_0603_1608Metric; LCSC Part Number C57112
D13: 1N4148; D_SOD-123
J6: RCV_SYS; Molex_Micro-Fit_3.0_43045-0412_2x02_P3.00mm_Vertical
J7: RBF_SYS; AudioJack_Vertical
Q8: AO3400A; SOT-23
R32: TBD; R_0603_1608Metric
R33: 10k; R_0603_1608Metric; LCSC Part Number C25804
R34: 1k; R_0603_1608Metric; LCSC Part Number C21190

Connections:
BRS_RBF: R34.1; also elsewhere on the board
BRS_RCV: Q8.1 (G); also elsewhere on the board
GND: C32.2, J7.1 (S), Q8.2 (S); also elsewhere on the board
HV_PWR_IN: D13.1 (K), J6.2, J6.4; also elsewhere on the board
unnamed: D13.2 (A), J6.1, J6.3, R32.1
unnamed: C32.1, J7.2 (T), J7.4 (TS), R33.1, R34.2
unnamed: Q8.3 (D), R32.2
VDD: R33.2; also elsewhere on the board

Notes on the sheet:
RBF Connected: BRS_RBF is LOW (0V) RBF Removed: BRS_RBF is HIGH (3.3V)
I_{D_max} = 5.8 A Compatible with both electromagnets and pyro charges

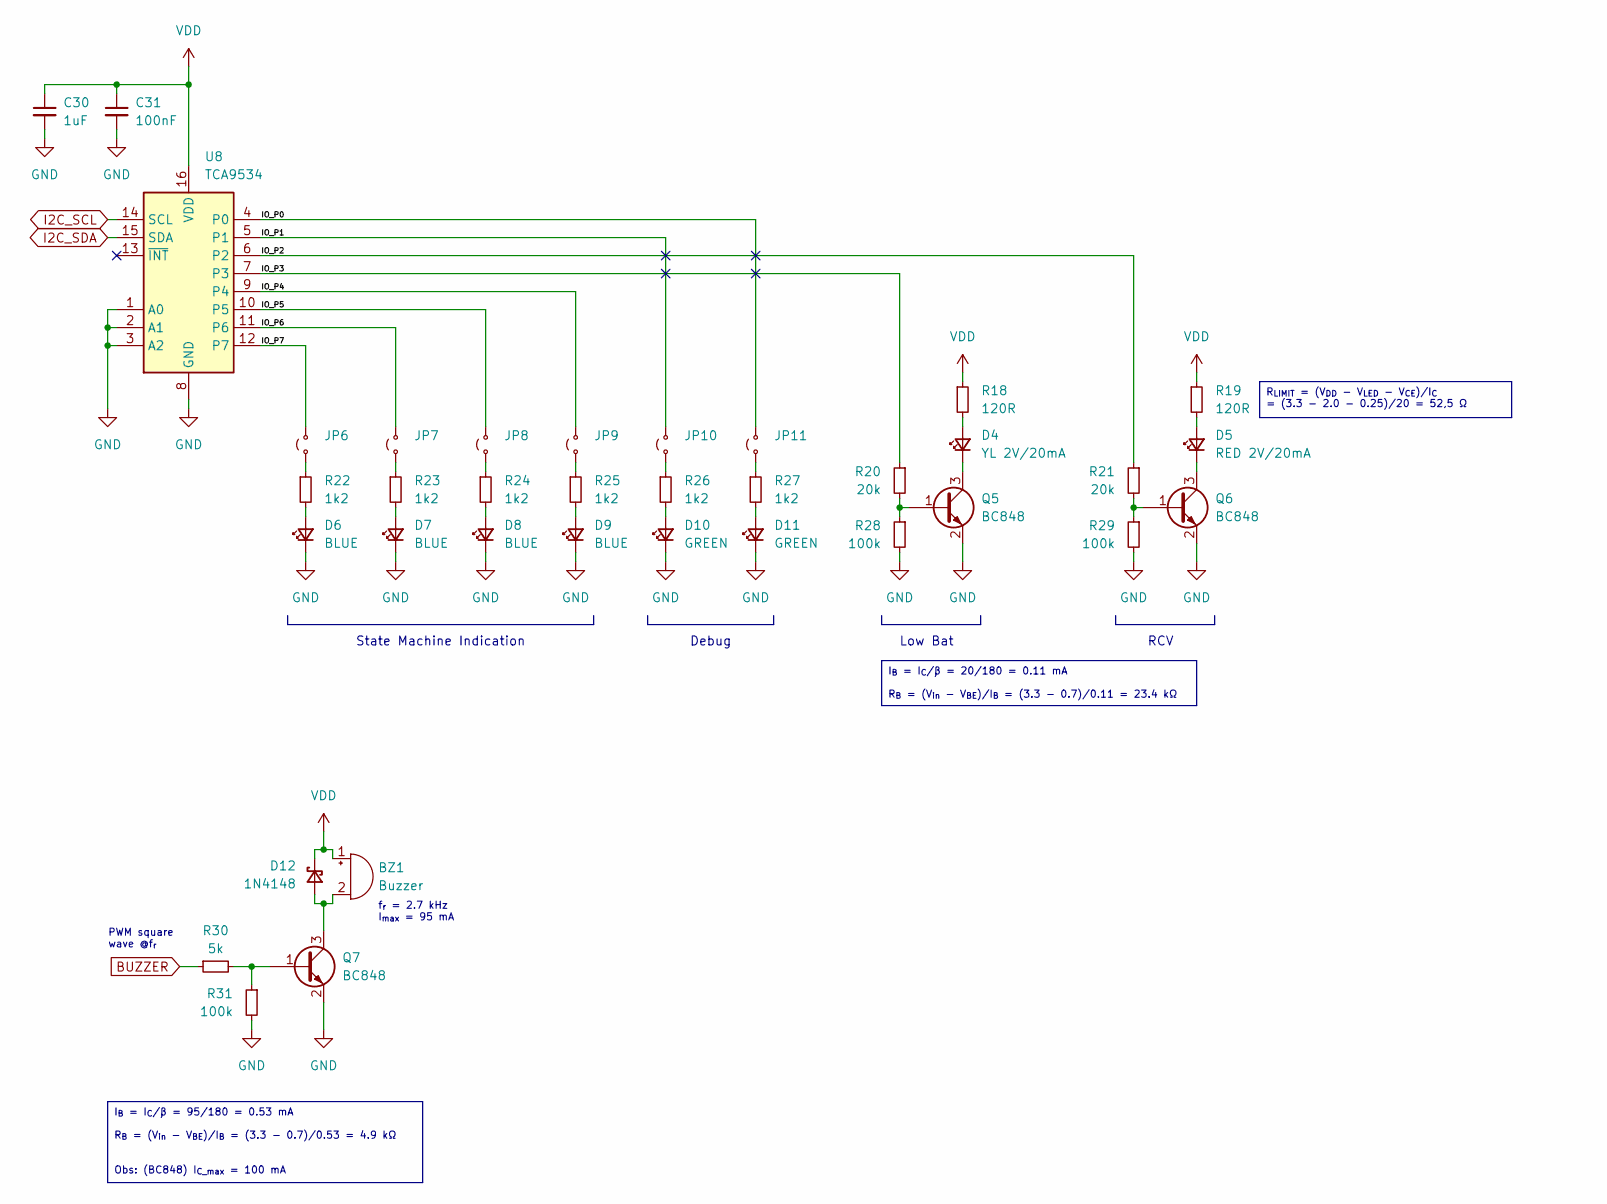
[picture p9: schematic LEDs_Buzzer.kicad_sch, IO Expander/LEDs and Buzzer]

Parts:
BZ1: Buzzer; PUIAudio_SMT_0825_S_4_R
C30: 1uF; C_0603_1608Metric; LCSC Part Number C57112
C31: 100nF; C_0603_1608Metric; LCSC Part Number C57112
D4: YL 2V/20mA; LED_0805_2012Metric
D5: RED 2V/20mA; LED_0805_2012Metric
D6, D7, D8, D9: BLUE; LED_0603_1608Metric
D10, D11: GREEN; LED_0603_1608Metric
D12: 1N4148; D_SOD-123
JP6, JP7, JP8, JP9, JP10, JP11: Jumper_2_Small_Open; SMD_SolderJumper_Small
Q5, Q6, Q7: BC848; SOT-23
R18, R19: 120R; R_0603_1608Metric
R20, R21: 20k; R_0603_1608Metric
R22, R23, R24, R25, R26, R27: 1k2; R_0603_1608Metric
R28, R29, R31: 100k; R_0603_1608Metric
R30: 5k; R_0603_1608Metric
U8: TCA9534; TSSOP-16_4.4x5mm_P0.65mm

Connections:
/Peripherals/LEDs_Buzzer/IO_P0: JP11.2 (B), U8.4 (P0)
/Peripherals/LEDs_Buzzer/IO_P1: JP10.2 (B), U8.5 (P1)
/Peripherals/LEDs_Buzzer/IO_P2: R21.1, U8.6 (P2)
/Peripherals/LEDs_Buzzer/IO_P3: R20.1, U8.7 (P3)
/Peripherals/LEDs_Buzzer/IO_P4: JP9.2 (B), U8.9 (P4)
/Peripherals/LEDs_Buzzer/IO_P5: JP8.2 (B), U8.10 (P5)
/Peripherals/LEDs_Buzzer/IO_P6: JP7.2 (B), U8.11 (P6)
/Peripherals/LEDs_Buzzer/IO_P7: JP6.2 (B), U8.12 (P7)
BUZZER: R30.1; also elsewhere on the board
GND: C30.2, C31.2, D6.1 (K), D7.1 (K), D8.1 (K), D9.1 (K), D10.1 (K), D11.1 (K), Q5.2 (E), Q6.2 (E), Q7.2 (E), R28.2, R29.2, R31.2, U8.1 (A0), U8.2 (A1), U8.3 (A2), U8.8 (GND); also elsewhere on the board
I2C_SCL: U8.14 (SCL); also elsewhere on the board
I2C_SDA: U8.15 (SDA); also elsewhere on the board
unnamed: BZ1.2 (-), D12.2 (A), Q7.3 (C)
unnamed: D4.2 (A), R18.2
unnamed: D4.1 (K), Q5.3 (C)
unnamed: D5.2 (A), R19.2
unnamed: D5.1 (K), Q6.3 (C)
unnamed: D6.2 (A), R22.2
unnamed: D7.2 (A), R23.2
unnamed: D8.2 (A), R24.2
unnamed: D9.2 (A), R25.2
unnamed: D10.2 (A), R26.2
unnamed: D11.2 (A), R27.2
unnamed: JP6.1 (A), R22.1
unnamed: JP7.1 (A), R23.1
unnamed: JP8.1 (A), R24.1
unnamed: JP9.1 (A), R25.1
unnamed: JP10.1 (A), R26.1
unnamed: JP11.1 (A), R27.1
unnamed: Q5.1 (B), R20.2, R28.1
unnamed: Q6.1 (B), R21.2, R29.1
unnamed: Q7.1 (B), R30.2, R31.1
VDD: BZ1.1 (+), C30.1, C31.1, D12.1 (K), R18.1, R19.1, U8.16 (VDD); also elsewhere on the board

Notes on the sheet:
R_{LIMIT} = (V_{DD} - V_{LED} - V_{CE})/I_{C} = (3.3 - 2.0 - 0.25)/20 = 52,5 Ω
I_{B} = I_{C}/β = 95/180 = 0.53 mA R_{B} = (V_{in} - V_{BE})/I_{B} = (3.3 - 0.7)/0.53 = 4.9 kΩ Obs: (BC848) I_{C_max} = 100 mA
I_{B} = I_{C}/β = 20/180 = 0.11 mA R_{B} = (V_{in} - V_{BE})/I_{B} = (3.3 - 0.7)/0.11 = 23.4 kΩ
Low Bat
PWM square wave @f_{r}
f_{r} = 2.7 kHz I_{max} = 95 mA
State Machine Indication
Debug
RCV

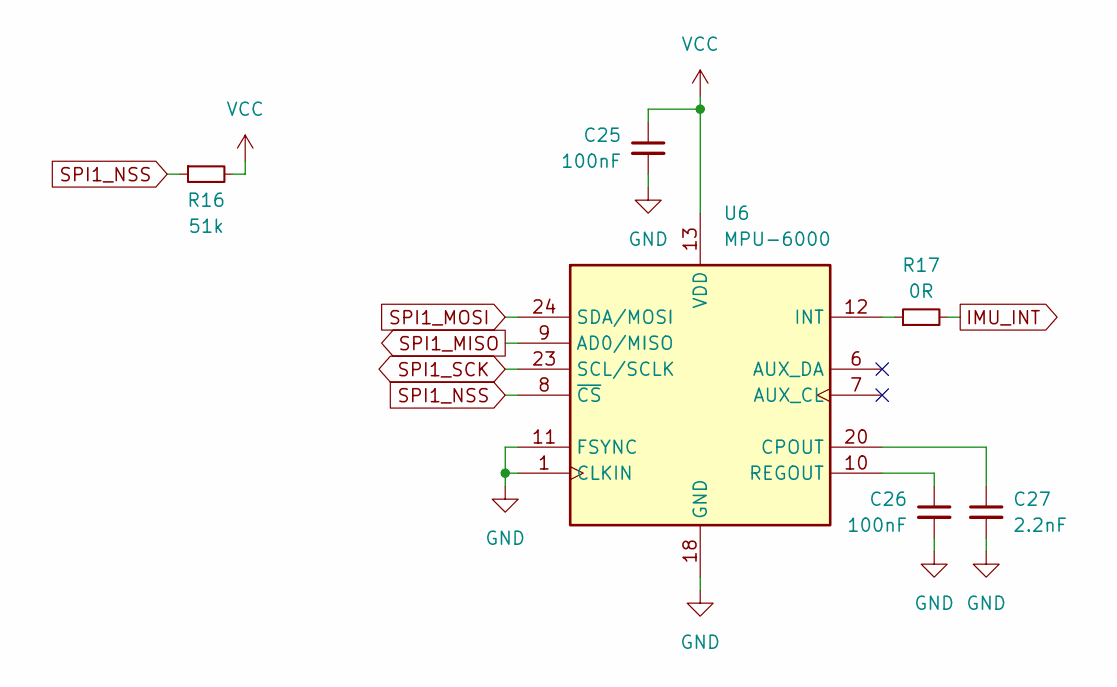
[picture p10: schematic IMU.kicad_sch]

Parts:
C25, C26: 100nF; C_0603_1608Metric; LCSC Part Number C57112
C27: 2.2nF; C_0603_1608Metric; LCSC Part Number C57112
R16: 51k; R_0603_1608Metric
R17: 0R; R_0603_1608Metric
U6: MPU-6000; InvenSense_QFN-24_4x4mm_P0.5mm

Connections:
GND: C25.2, C26.2, C27.2, U6.1 (CLKIN), U6.11 (FSYNC), U6.18 (GND); also elsewhere on the board
IMU_INT: R17.2; also elsewhere on the board
unnamed: C27.1, U6.20 (CPOUT)
unnamed: R17.1, U6.12 (INT)
unnamed: C26.1, U6.10 (REGOUT)
SPI1_MISO: U6.9 (AD0/MISO); also elsewhere on the board
SPI1_MOSI: U6.24 (SDA/MOSI); also elsewhere on the board
SPI1_NSS: R16.1, U6.8 (~CS); also elsewhere on the board
SPI1_SCK: U6.23 (SCL/SCLK); also elsewhere on the board
VCC: C25.1, R16.2, U6.13 (VDD); also elsewhere on the board

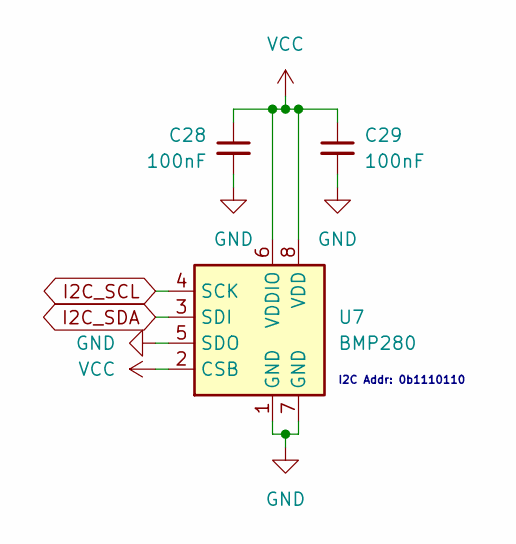
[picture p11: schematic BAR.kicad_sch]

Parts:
C28, C29: 100nF; C_0402_1005Metric; LCSC Part Number C57112
U7: BMP280; Bosch_LGA-8_2x2.5mm_P0.65mm_ClockwisePinNumbering

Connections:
GND: C28.2, C29.2, U7.1 (GND), U7.5 (SDO), U7.7 (GND); also elsewhere on the board
I2C_SCL: U7.4 (SCK); also elsewhere on the board
I2C_SDA: U7.3 (SDI); also elsewhere on the board
VCC: C28.1, C29.1, U7.2 (CSB), U7.6 (VDDIO), U7.8 (VDD); also elsewhere on the board

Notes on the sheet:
I2C Addr: 0b1110110

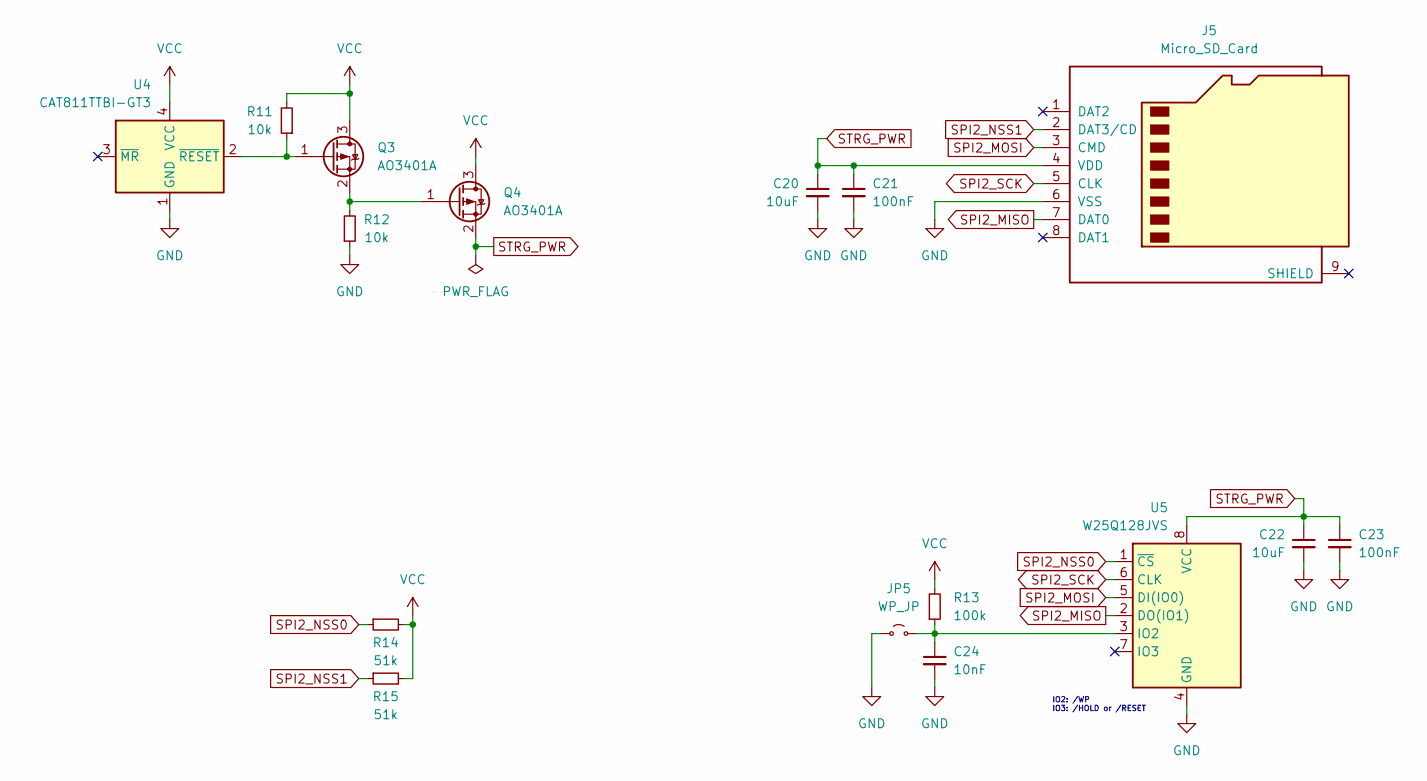
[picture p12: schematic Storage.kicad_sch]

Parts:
C20, C22: 10uF; C_0603_1608Metric; LCSC Part Number C57112
C21, C23: 100nF; C_0603_1608Metric; LCSC Part Number C57112
C24: 10nF; C_0603_1608Metric; LCSC Part Number C57112
J5: Micro_SD_Card; microSD_HC_Wuerth_693072010801
JP5: WP_JP; PinHeader_1x02_P2.54mm_Vertical
Q3, Q4: AO3401A; SOT-23
R11, R12: 10k; R_0603_1608Metric
R13: 100k; R_0603_1608Metric
R14, R15: 51k; R_0603_1608Metric
U4: CAT811TTBI-GT3; SOT-143
U5: W25Q128JVS; SOIC-8_5.23x5.23mm_P1.27mm

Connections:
GND: C20.2, C21.2, C22.2, C23.2, C24.2, J5.6 (VSS), JP5.1 (A), R12.1, U4.1 (GND), U5.4 (GND); also elsewhere on the board
unnamed: C24.1, JP5.2 (B), R13.1, U5.3 (IO2)
unnamed: Q3.1 (G), R11.1, U4.2 (~RESET)
unnamed: Q3.2 (S), Q4.1 (G), R12.2
SPI2_MISO: J5.7 (DAT0), U5.2 (DO(IO1)); also elsewhere on the board
SPI2_MOSI: J5.3 (CMD), U5.5 (DI(IO0)); also elsewhere on the board
SPI2_NSS0: R14.1, U5.1 (~CS); also elsewhere on the board
SPI2_NSS1: J5.2 (DAT3/CD), R15.1; also elsewhere on the board
SPI2_SCK: J5.5 (CLK), U5.6 (CLK); also elsewhere on the board
STRG_PWR: C20.1, C21.1, C22.1, C23.1, J5.4 (VDD), Q4.2 (S), U5.8 (VCC)
VCC: Q3.3 (D), Q4.3 (D), R11.2, R13.2, R14.2, R15.2, U4.4 (VCC); also elsewhere on the board

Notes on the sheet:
IO2: /WP IO3: /HOLD or /RESET

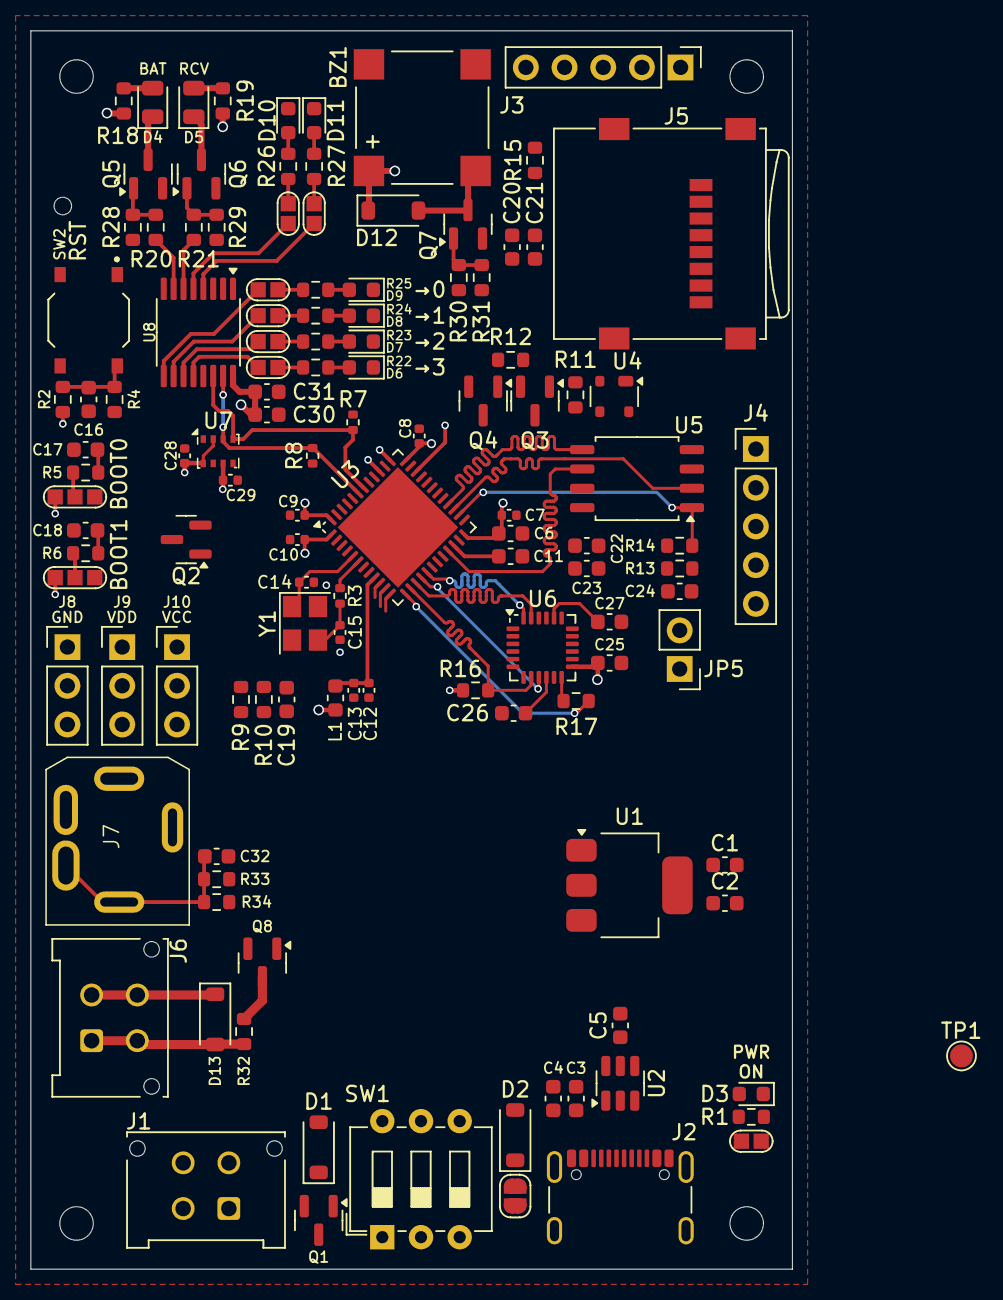
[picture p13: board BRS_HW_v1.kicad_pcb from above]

Board: 6 copper layers, 50.0 x 81.3 mm, 129 parts (0 on the bottom side), 90 nets.

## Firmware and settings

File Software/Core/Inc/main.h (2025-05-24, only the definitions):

#define ADC_BAT_Pin GPIO_PIN_0
#define ADC_BAT_GPIO_Port GPIOA
#define BRS_RBF_Pin GPIO_PIN_1
#define BRS_RBF_GPIO_Port GPIOA
#define BRS_RCV_Pin GPIO_PIN_2
#define BRS_RCV_GPIO_Port GPIOA
#define IMU_INT_Pin GPIO_PIN_3
#define IMU_INT_GPIO_Port GPIOA
#define BOOT1_Pin GPIO_PIN_2
#define BOOT1_GPIO_Port GPIOB
#define SPI2_NSS1_Pin GPIO_PIN_12
#define SPI2_NSS1_GPIO_Port GPIOB
#define SPI2_NSS0_Pin GPIO_PIN_13
#define SPI2_NSS0_GPIO_Port GPIOB
#define BUZZER_Pin GPIO_PIN_4
#define BUZZER_GPIO_Port GPIOB
#define SENS_PWR_Pin GPIO_PIN_8
#define SENS_PWR_GPIO_Port GPIOB
#define BOARD_PWR_Pin GPIO_PIN_9
#define BOARD_PWR_GPIO_Port GPIOB

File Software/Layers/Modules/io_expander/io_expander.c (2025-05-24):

/**
 **************************************************************************************************
 * @file           : io_expander.c
 * @brief          : IO Expander driver
 **************************************************************************************************
 * @author         : Lucas Noce
 * @date           : 2025/02/05
 * @version        : v1.0
 **************************************************************************************************
 * @copyright
 * MIT License
 *
 * Copyright (c) 2025 Lucas Noce
 *
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
 * THE SOFTWARE IS PROVIDED "AS IS", WITHOUT WARRANTY OF ANY KIND, EXPRESS OR IMPLIED, INCLUDING
 * BUT NOT LIMITED TO THE WARRANTIES OF MERCHANTABILITY, FITNESS FOR A PARTICULAR PURPOSE AND
 * NONINFRINGEMENT. IN NO EVENT SHALL THE AUTHORS OR COPYRIGHT HOLDERS BE LIABLE FOR ANY CLAIM,
 * DAMAGES OR OTHER LIABILITY, WHETHER IN AN ACTION OF CONTRACT, TORT OR OTHERWISE, ARISING FROM,
 * OUT OF OR IN CONNECTION WITH THE SOFTWARE OR THE USE OR OTHER DEALINGS IN THE SOFTWARE.
 **************************************************************************************************
 * @note
 * - STM32 Series: STM32F411xx (Update as needed)
 * - Toolchain: STM32CubeMX / VS Code + STM32 VS Code Extension + CMake
 **************************************************************************************************
 */


#include "../../Modules/io_expander/io_expander.h"

#include <stdint.h>
#include <stdbool.h>

#include "../../Utilities/brs_errno.h"
#include "../../BSP/bsp_i2c.h"


/* Definitions ================================================================================= */

#define IO_EXPANDER_STD_TIMEOUT 100

/* Enums ======================================================================================= */



/* Typedefs ==================================================================================== */

/*!
  @brief        Current state of IO Expander.

  @param        input: input value of each GPIO.
  @param        output: output value of each GPIO.
  @param        polarity: polarity value of each GPIO.
  @param        direction: direction value of each GPIO.
*/
typedef struct IO_EXPANDER_DATA_TAG{
  uint8_t input;
  uint8_t output;
  uint8_t polarity;
  uint8_t direction;
} IO_EXPANDER_DATA_T;

/* Static Variables ============================================================================ */

static IO_EXPANDER_DATA_T io_expander_data;

static bool io_expander_driver_init = false;

/* Local Function Prototypes =================================================================== */

/*!
  @brief        Change a specific bit on a data byte.

  @param[out]   p_data: pointer to the variable to be changed.
  @param[in]    val: value to be written on the data variable's bit position.
  @param[in]    bit: the bit position.

  @returns      void.
*/
static inline void _io_expander_set_data_bit( uint8_t *p_data, uint8_t val, uint8_t bit );

/*!
  @brief        Writes a byte to a register through STM32 HAL_I2C.

  @param[in]    reg: the IO Expander register to be written.
  @param[in]    p_data: pointer to the data to be written.

  @returns      0 if success, `BRS_ERR_[]` otherwise (see brs_errno.h).
*/
static inline int8_t _io_expander_i2c_write( uint8_t reg, uint8_t *p_data );

/* Global Functions Implementation ============================================================= */

int8_t io_expander_init( void ){
  int8_t ret = BRS_RET_OK;

  if( io_expander_driver_init )
    return BRS_RET_OK;

  ret = io_expander_config( IO_EXPANDER_ALL_GPIOS,
                            ~( IO_EXPANDER_REG_VAL_DIRECTION_INPUT - 1 ),
                            ~( IO_EXPANDER_REG_VAL_POLARITY_NORMAL - 1 ) );  // ~0 = 0xFF and ~(-1) = 0x00

  if( ret == 0 )
    io_expander_driver_init = true;

  return ret;
}

int8_t io_expander_config( uint8_t gpio, uint8_t direction, uint8_t polarity ){
  int8_t ret = BRS_RET_OK;

  if( !io_expander_driver_init )
    return BRS_ERR_NOT_INIT;

  if( gpio > IO_EXPANDER_ALL_GPIOS ){
    return BRS_ERR_INVALID_PARAM;
  }
  else if( gpio == IO_EXPANDER_ALL_GPIOS ){
    io_expander_data.direction = direction;
    io_expander_data.polarity  = polarity;
  }
  else{
    _io_expander_set_data_bit( &io_expander_data.direction, ( direction & 0x01 ), gpio );
    _io_expander_set_data_bit( &io_expander_data.polarity, ( polarity & 0x01 ), gpio );
  }

  ret += _io_expander_i2c_write( IO_EXPANDER_CMD_REG_DIRECTION, &io_expander_data.direction );
  ret += _io_expander_i2c_write( IO_EXPANDER_CMD_REG_POLARITY, &io_expander_data.polarity );

  return ret;
}

int8_t io_expander_write( uint8_t gpio, uint8_t value ){
  int8_t ret = BRS_RET_OK;

  if( !io_expander_driver_init )
    return BRS_ERR_NOT_INIT;

  if( gpio > IO_EXPANDER_ALL_GPIOS ){
    return BRS_ERR_INVALID_PARAM;
  }
  else if( gpio == IO_EXPANDER_ALL_GPIOS ){
    io_expander_data.output = value;
  }
  else{
    _io_expander_set_data_bit( &io_expander_data.output, ( value & 0x01 ), gpio );
  }

  ret = _io_expander_i2c_write( IO_EXPANDER_CMD_REG_DIRECTION, &io_expander_data.output );

  return ret;
}

/* Local Functions Implementation ============================================================== */

static inline void _io_expander_set_data_bit( uint8_t *p_data, uint8_t val, uint8_t bit ){
  *p_data = ( ( *p_data & ~( 1 << bit ) ) | ( ( val & 0x01 ) << bit ) );
}

static inline int8_t _io_expander_i2c_write( uint8_t reg, uint8_t *p_data ){
  return bsp_i2c_write_reg( IO_EXPANDER_I2C_ADDR, reg, p_data );
}

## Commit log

2025-02-05 Adding stm32 project files
2025-02-05 Moved stm32 project into repo root folder
2025-02-05 Implementing IO Expander driver
2025-02-06 Implemented IO Expander driver
2025-02-13 Adding HW design
    [BAR.kicad_sch, BRS_HW_v1.kicad_pcb, BRS_HW_v1.kicad_sch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]
2025-02-13 Developing HW
    [BAR.kicad_sch, IMU.kicad_sch, LEDs_Buzzer.kicad_sch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]
2025-02-14 Developing HW - routing
    [BRS_HW_v1.kicad_pcb, LEDs_Buzzer.kicad_sch, MCU.kicad_sch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]

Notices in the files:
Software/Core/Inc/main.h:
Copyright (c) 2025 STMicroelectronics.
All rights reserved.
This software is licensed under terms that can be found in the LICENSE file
